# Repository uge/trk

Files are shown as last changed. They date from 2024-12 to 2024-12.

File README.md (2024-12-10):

# nrf9151 based picoballoon tracker in kicad

This repo contains a KiCad 8.0 project which hopes to implement a low power tracker for pico-balloons
based on the nRF9151 module and a WSPR protocol modulator.

## Why the nRF9151?

The nRF9151 is marketed with emphasis on cellular data and GPS capabilities with optimization for power.
Trackers are one category of intended applications and the device and software stack have provisions for 
aggressive power saving modes. Even if the cellular data connectivity feature is not used, the nrf9151
is a power efficient microcontroller with an embedded GPS.

The cellular functionality opens up the possibility of eventually using NTN services such as Skylo or Starlink.

## WSPR modulator

The Si5351 is a common frequency synthesizer used to implement the WSPR protocol. This design opts
for the TI CDCE6214 in hopes of reducing power consumption and to try something different.

## Power conversion

Following the Traquito's example, this design uses buck-boost converters to adapt to varying and lower voltages.
This design uses the TI TPS631010 which can operate at input voltages from 1.6V to 5.5V. There are two
buck-boost converters for the 1.8V and 3.3V supplies respectively.

## Manufacturing

This design is targeted at JLCPCB 4 layer design rules and includes JLCPCB part numbers in the BOM.

## License and Copyright

Copyright 2024 - Eugene Feinberg (ugeook at gmail dot com)

Licensed under Creative Commons Attribution-NonCommercial 4.0 International Public License

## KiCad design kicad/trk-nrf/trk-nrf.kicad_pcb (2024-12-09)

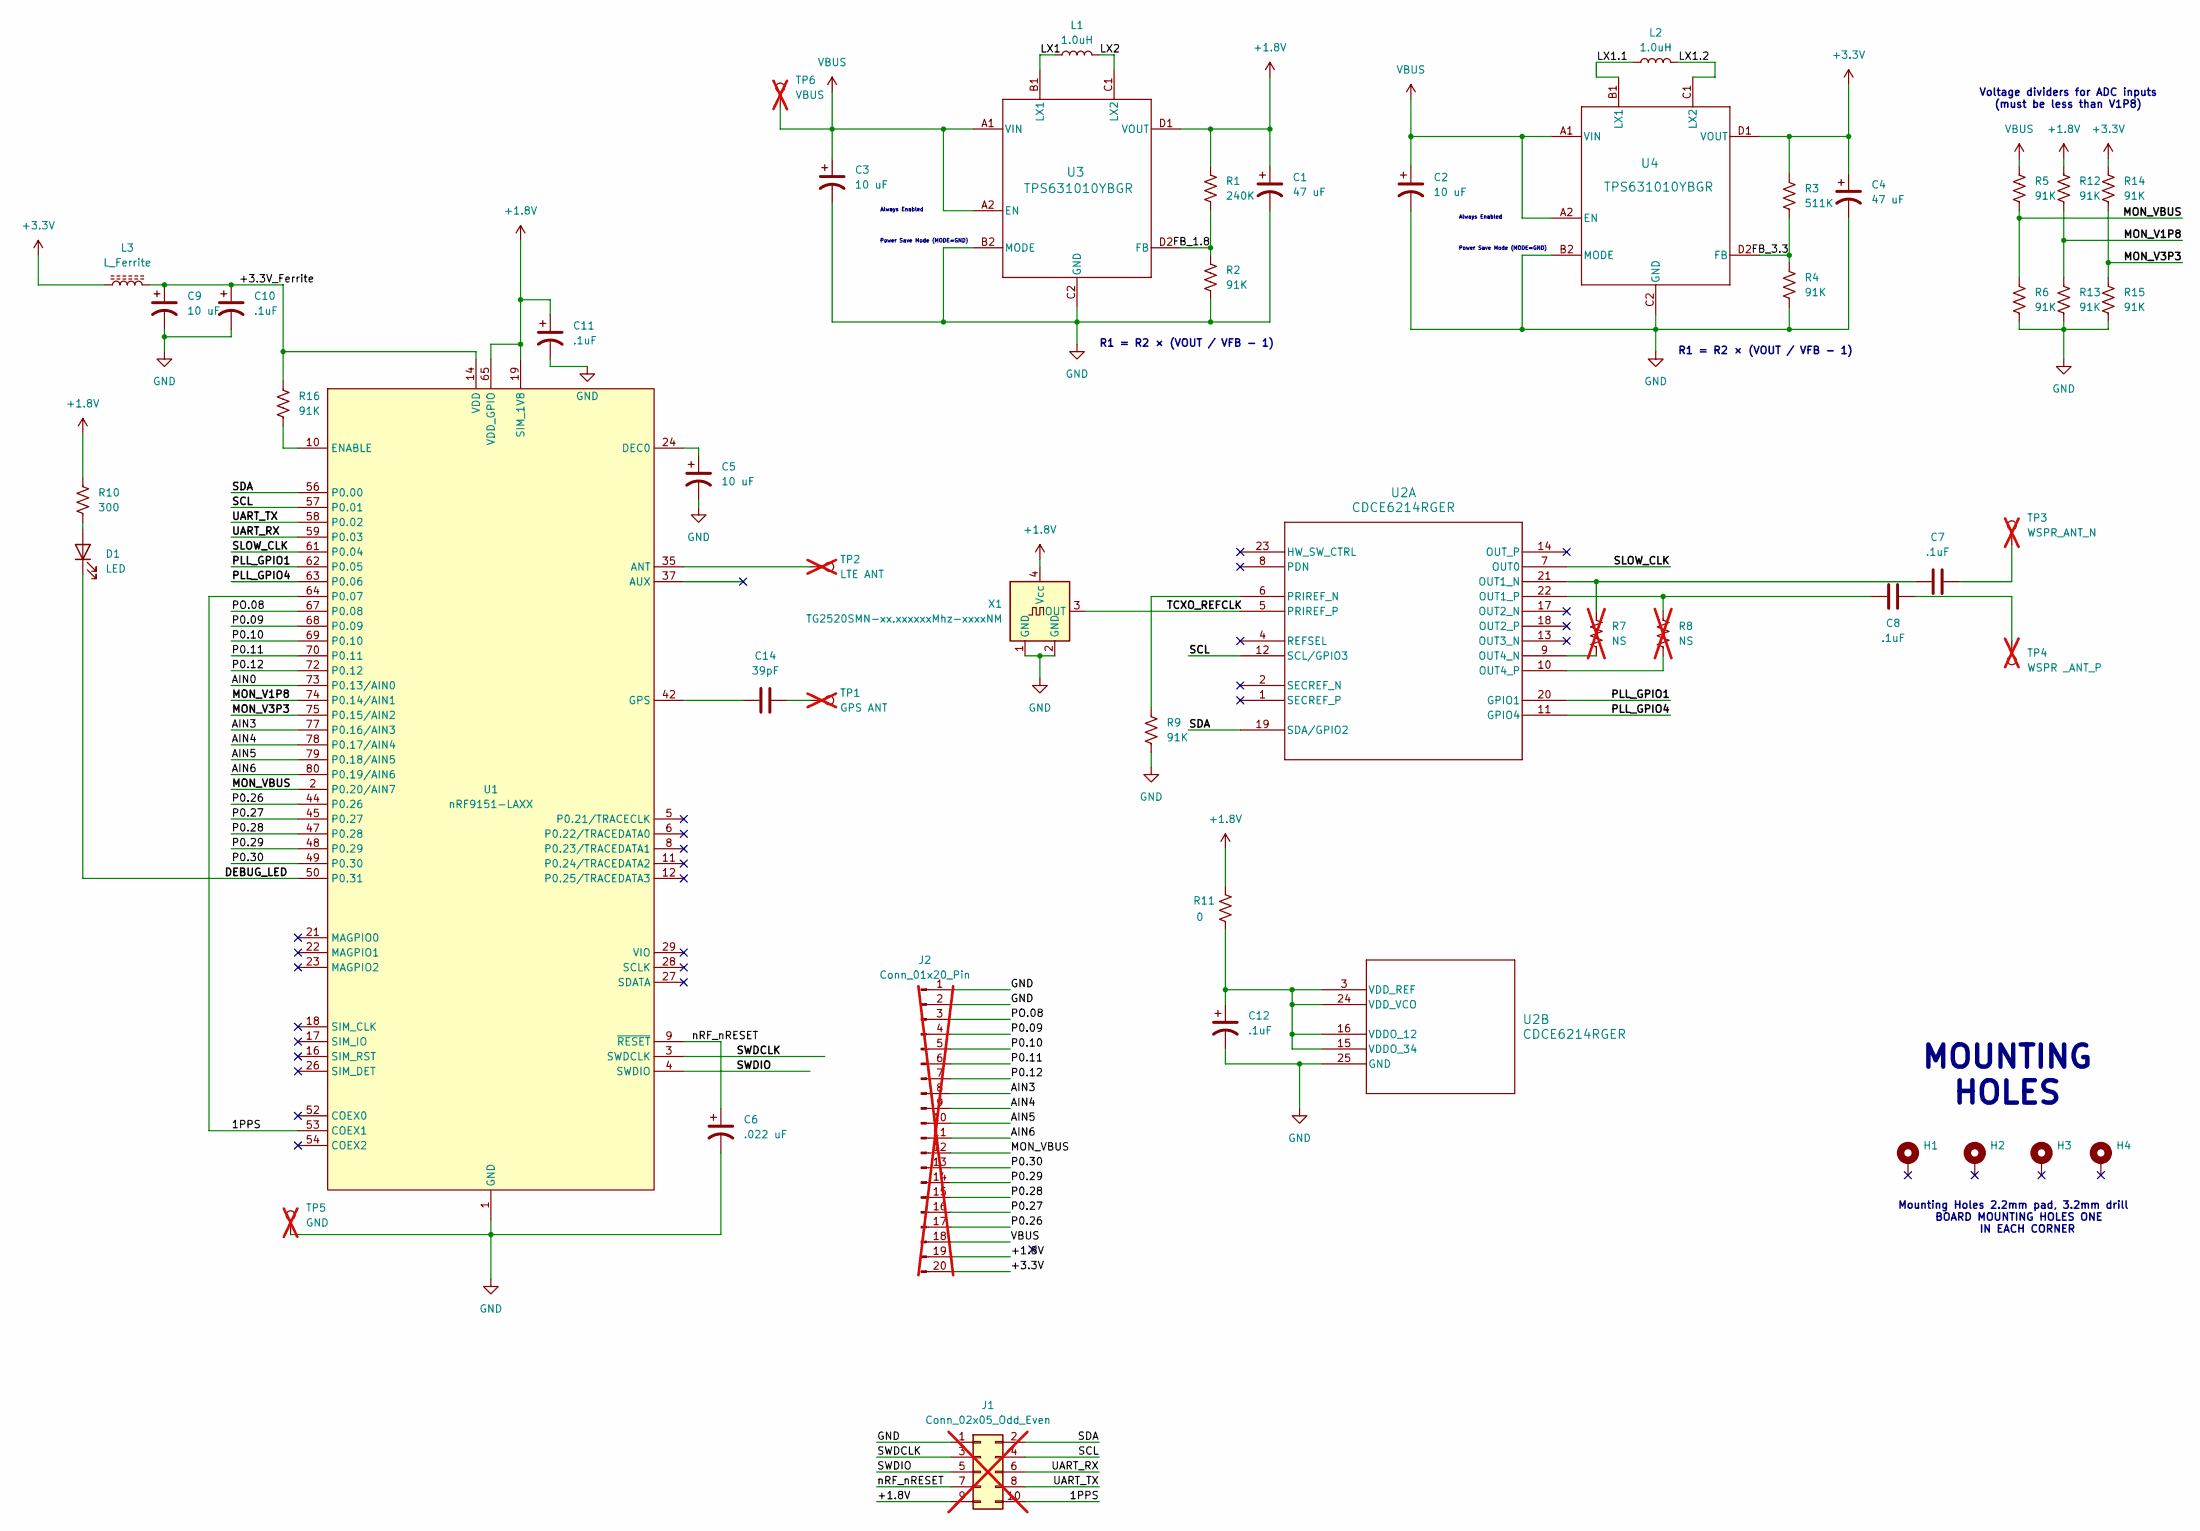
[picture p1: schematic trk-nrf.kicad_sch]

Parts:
C1, C4: 47 uF; C_0805_2012Metric; JLCPCB Part Number C16780
C2, C3, C5, C9: 10 uF; C_0603_1608Metric; JLCPCB Part Number C1691
C6: .022 uF; C_0402_1005Metric; JLCPCB Part Number C60474
C7, C8, C10, C11, C12: .1uF; C_0402_1005Metric; JLCPCB Part Number C1525
C14: 39pF; C_0402_1005Metric; JLCPCB Part Number C342946
D1: LED; LED_0402_1005Metric; JLCPCB Part Number C3007519
H1, H2, H3, H4: MountingHole_Pad_MP; MountingHole_2.2mm_M2_ISO7380_Pad
J1: Conn_02x05_Odd_Even; PinHeader_2x05_P1.00mm_Vertical_SMD; not fitted
J2: Conn_01x20_Pin; Hirose_FH12-20S-0.5SH_1x20-1MP_P0.50mm_Horizontal; not fitted
L1, L2: 1.0uH; L_Murata_DFE201610P; JLCPCB Part Number C92921
L3: L_Ferrite; L_0805_2012Metric; JLCPCB Part Number C12389
R1: 240K; R_0402_1005Metric; JLCPCB Part Number C64043
R2, R4, R5, R6, R9, R12, R13, R14, R15, R16: 91K; R_0402_1005Metric; JLCPCB Part Number C25573
R3: 511K; R_0402_1005Metric; JLCPCB Part Number C64042
R7, R8: NS; R_0402_1005Metric; not fitted
R10: 300; R_0402_1005Metric; JLCPCB Part Number C25159
R11: 0; R_0402_1005Metric; JLCPCB Part Number C17168
TP1: GPS ANT; TestPoint_Pad_1.5x1.5mm; not fitted
TP2: LTE ANT; TestPoint_Pad_1.5x1.5mm; not fitted
TP3: WSPR_ANT_N; TestPoint_THTPad_D1.5mm_Drill0.7mm; not fitted
TP4: WSPR _ANT_P; TestPoint_THTPad_D1.5mm_Drill0.7mm; not fitted
TP5: GND; TestPoint_THTPad_D1.5mm_Drill0.7mm; not fitted
TP6: VBUS; TestPoint_THTPad_D1.5mm_Drill0.7mm; not fitted
U1: nRF9151-LAXX; LGA_9151_12.1x11.1mm; JLCPCB Part Number C22397843
U2: CDCE6214RGER; VQFN24_RGE_TEX; JLCPCB Part Number C3608351
U3, U4: TPS631010YBGR; YBG0008; JLCPCB Part Number C6719123
X1: TG2520SMN-xx.xxxxxxMhz-xxxxNM; Oscillator_SMD_SeikoEpson_TG2520SMN-xxx-xxxxxx-4Pin_2.5x2.0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; JLCPCB Part Number C5590921

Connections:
+1.8V: C1.1, C11.1, J1.9, J2.19, R1.1, R10.1, R11.1, R12.1, U1.19 (SIM_1V8), U1.65 (VDD_GPIO), U3.D1 (VOUT), X1.4 (Vcc)
+3.3V: C4.1, J2.20, L3.1, R3.1, R14.1, U4.D1 (VOUT)
/1PPS: J1.10, U1.53 (COEX1), U1.64 (P0.07)
/+3.3V_Ferrite: C9.1, C10.1, L3.2, R16.1, U1.14 (VDD)
/AIN0: U1.73 (P0.13/AIN0)
/AIN3: J2.8, U1.77 (P0.16/AIN3)
/AIN4: J2.9, U1.78 (P0.17/AIN4)
/AIN5: J2.10, U1.79 (P0.18/AIN5)
/AIN6: J2.11, U1.80 (P0.19/AIN6)
/DEBUG_LED: D1.1 (K), U1.50 (P0.31)
/FB_1.8: R1.2, R2.1, U3.D2 (FB)
/FB_3.3: R3.2, R4.1, U4.D2 (FB)
/LX1: L1.1, U3.B1 (LX1)
/LX1.1: L2.1, U4.B1 (LX1)
/LX1.2: L2.2, U4.C1 (LX2)
/LX2: L1.2, U3.C1 (LX2)
/MON_V1P8: R12.2, R13.1, U1.74 (P0.14/AIN1)
/MON_V3P3: R14.2, R15.1, U1.75 (P0.15/AIN2)
/MON_VBUS: J2.12, R5.2, R6.1, U1.2 (P0.20/AIN7)
/P0.09: J2.4, U1.68 (P0.09)
/P0.10: J2.5, U1.69 (P0.10)
/P0.11: J2.6, U1.70 (P0.11)
/P0.12: J2.7, U1.72 (P0.12)
/P0.26: J2.17, U1.44 (P0.26)
/P0.27: J2.16, U1.45 (P0.27)
/P0.28: J2.15, U1.47 (P0.28)
/P0.29: J2.14, U1.48 (P0.29)
/P0.30: J2.13, U1.49 (P0.30)
/PLL_GPIO1: U1.62 (P0.05), U2.20 (GPIO1)
/PLL_GPIO4: U1.63 (P0.06), U2.11 (GPIO4)
/PO.08: J2.3, U1.67 (P0.08)
/SCL: J1.4, U1.57 (P0.01), U2.12 (SCL/GPIO3)
/SDA: J1.2, U1.56 (P0.00), U2.19 (SDA/GPIO2)
/SLOW_CLK: U1.61 (P0.04), U2.7 (OUT0)
/SWDCLK: J1.3, U1.3 (SWDCLK)
/SWDIO: J1.5, U1.4 (SWDIO)
/TCXO_REFCLK: U2.5 (PRIREF_P), X1.3 (OUT)
/UART_RX: J1.6, U1.59 (P0.03)
/UART_TX: J1.8, U1.58 (P0.02)
/nRF_nRESET: C6.1, J1.7, U1.9 (~RESET)
GND: C1.2, C2.2, C3.2, C4.2, C5.2, C6.2, C9.2, C10.2, C11.2, C12.2, J1.1, J2.1, J2.2, R2.2, R4.2, R6.2, R9.2, R13.2, R15.2, TP5.1, U1.1 (GND), U1.7 (GND), U1.13 (GND), U1.15 (GND), U1.20 (GND), U1.25 (GND), U1.30 (GND), U1.34 (GND), U1.36 (GND), U1.38 (GND), U1.39 (GND), U1.40 (GND), U1.41 (GND), U1.43 (GND), U1.46 (GND), U1.51 (GND), U1.55 (GND), U1.60 (GND), U1.66 (GND), U1.71 (GND), U1.76 (GND), U1.105 (GND), U1.106 (GND), U1.107 (GND), U1.108 (GND), U1.109 (GND), U1.110 (GND), U1.111 (GND), U1.112 (GND), U1.113 (GND), U2.25 (GND), U3.B2 (MODE), U3.C2 (GND), U4.B2 (MODE), U4.C2 (GND), X1.1 (GND), X1.2 (GND)
unnamed: C7.2, TP3.1
unnamed: C8.2, TP4.1
unnamed: C14.2, TP1.1
unnamed: D1.2 (A), R10.2
unnamed: TP2.1, U1.35 (ANT)
unnamed: C5.1, U1.24 (DEC0)
unnamed: R16.2, U1.10 (ENABLE)
unnamed: C14.1, U1.42 (GPS)
unnamed: C7.1, R7.1, U2.21 (OUT1_N)
unnamed: C8.1, R8.1, U2.22 (OUT1_P)
unnamed: R7.2, U2.9 (OUT4_N)
unnamed: R8.2, U2.10 (OUT4_P)
unnamed: R9.1, U2.6 (PRIREF_N)
unnamed: C12.1, R11.2, U2.3 (VDD_REF), U2.15 (VDDO_34), U2.16 (VDDO_12), U2.24 (VDD_VCO)
VBUS: C2.1, C3.1, J2.18, R5.1, TP6.1, U3.A1 (VIN), U3.A2 (EN), U4.A1 (VIN), U4.A2 (EN)

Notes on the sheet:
Mounting Holes 2.2mm pad, 3.2mm drill BOARD MOUNTING HOLES ONE IN EACH CORNER
MOUNTING HOLES
Power Save Mode (MODE=GND)
Always Enabled
R1 = R2 × (VOUT / VFB - 1)
Voltage dividers for ADC inputs (must be less than V1P8)

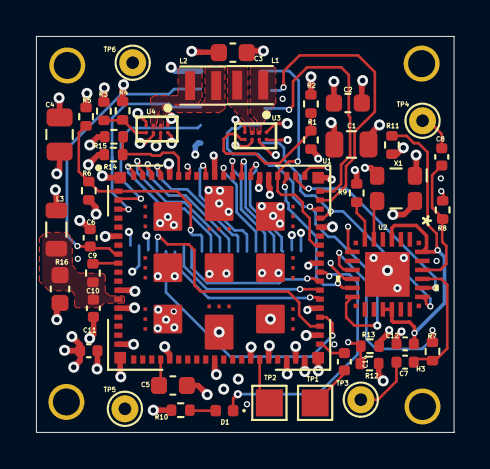
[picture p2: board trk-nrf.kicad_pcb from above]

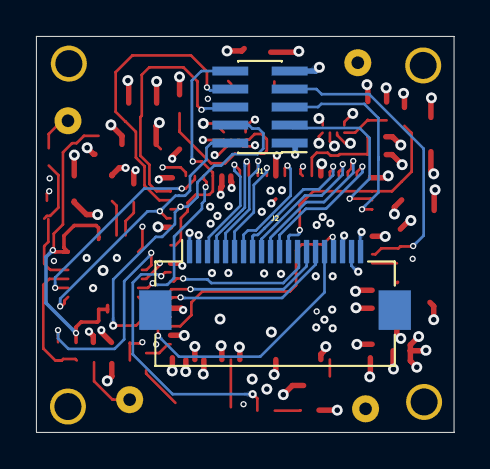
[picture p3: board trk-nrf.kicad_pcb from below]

Board: 4 copper layers, 23.2 x 22.0 mm, 50 parts (2 on the bottom side), 55 nets.

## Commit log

2024-11-29 Updates - pre-routing
    [trk-nrf.kicad_pcb, trk-nrf.kicad_sch]
2024-12-02 Schematic edits and drc changes
    [trk-nrf.kicad_pcb, trk-nrf.kicad_sch]
2024-12-02 Updated schematic
    [trk-nrf.kicad_pcb, trk-nrf.kicad_sch]
2024-12-04 Add second ground and freeroute board
    [trk-nrf.kicad_pcb, trk-nrf.kicad_sch]
2024-12-09 Board detailed routing by Estifanos Nega
    [trk-nrf.kicad_pcb, trk-nrf.kicad_sch]
